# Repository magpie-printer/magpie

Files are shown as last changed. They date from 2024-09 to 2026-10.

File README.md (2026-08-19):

# Magpie

The Magpie is an open source core XY 3D printer. It's mostly printed, and can largely be built of old printers that you may have already laying around.

Design is based off of an older Rolohaun Rook design, which can be found here: https://github.com/rolohaun/Rook-180

You can put a Prusa bed on it or an Ender 3 Bed, or most other beds that can mount to a piece of 2020 extrusion.

The print area is the same as an Ender 3, and you can print a Magpie on a printer as small as a Prusa Mini.

It incorporates a P1P-style Z-axis where 3 leadscrews are driven by a single NEMA 17 stepper motor.

You can use a p1p/P1s or X1 hotend for the toolhead.

Photo of the magpie 3D printer Magpie Printer

# Magpie Mod Hub

Check out community-built upgrades on the [live Mod Hub](https://magpie-printer.github.io/magpie/) (served via GitHub Pages) or browse the static files at [`mod-hub/`](mod-hub/index.html) inside this repo. The gallery is generated directly from the `Mods/` directory, so every accepted contribution automatically shows up in the showcase.

Want to publish your own mod? Follow the short submission guide in [`Mods/README.md`](Mods/README.md); it covers the required README format and how to regenerate the hub data.

# BOM

**BOM AVAILABLE HERE**

https://docs.google.com/spreadsheets/d/1rcG37SRJA-JKYnLYInnxDPbj7JWwB8L_99AdPJc4EQ8/edit?usp=sharing

It cost me about $200 for me to build one self sourced, but your mileage may vary. I got the price down by buying dead Ender 3's on Facebook marketplace.

# Print Your own T-Shirt

The Magpie is a new project, and I can't afford to be making T-shirts and handing them out to everybody that wants them (Though I'd like to) Still, there's no reason I can't give you the files to make one for yourself! https://drive.google.com/file/d/1uzCCMDghiNLJrrfc_lJbdbuVM2ewp0ao/view?usp=sharing


# DISCORD

**JOIN US ON DISCORD**

https://discord.gg/zkxYRuTDAA

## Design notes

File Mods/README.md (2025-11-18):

# 🐦 Magpie Mods

This directory is for user-created modifications and improvements for the [Magpie CoreXY 3D Printer](https://github.com/your-username/magpie-printer-project).

We encourage the community to contribute their own designs to enhance the functionality, aesthetics, or performance of the printer.

## 💡 How to Submit a Mod

To keep this repository organized and accessible, please follow these guidelines when submitting your mod:

### 1.  **Create a New Folder**
 All files for a single mod must be contained within a new folder. Please give your folder a descriptive name (e.g., `toolhead_fan_shroud`, `led_strip_mount`, `z-chain-mount`).

### 2.  **Provide a README.md** 
Inside your mod's folder, include a `README.md` file. The Mod Hub scrapes the first heading, first paragraph, and a `Made by:` line, so format your document accordingly. At minimum include:
    * A brief description of what your mod does (first paragraph after the title becomes the card summary).
    * A list of any additional hardware required (screws, nuts, wires, etc.).
    * Simple assembly instructions.
    * Any known issues or special considerations.
	* The name of the submitting author prefixed with `Made by:` so credit appears correctly.

### 3. ** PLEASE Include `.step` Files In your submission ** 
**We require all part files to be submitted in the `.step` format. You can include other things if you want, but STEP has to be in there!**

#### **Why STEP?**

The Magpie project is built on the principle of open collaboration and easy modification. By using the `.step` format, we ensure that every user can:
  * **Freely Modify:** Edit the parts in any major CAD software (Fusion 360, SolidWorks, Onshape, FreeCAD, etc.) without losing design history or running into proprietary format issues.
  * **Learn and Improve:** Analyze the part designs to understand how they work and invent new, better parts for the printer.
  * **Maintain Compatibility:** Avoid problems with different versions of software and proprietary file formats.

 **Note:** Please do not submit `.stl`, `.3mf`, or other mesh files in lieu of a proper STEP file.
 <br>
     – These files are useful for printing but are difficult to modify and are counter to the project's goal of easy design collaboration.

-----
## ⚖️ License

All mods submitted to this folder are subject to the same license as the main Magpie printer project. By submitting a pull request, you agree to this.

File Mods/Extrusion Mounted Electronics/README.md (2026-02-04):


# Extrusion Mounted Electronics

## Summary
Mount electronics to the rear extrusion of the Magpie so you don't have to laser cut acrylic.

Made by: SpiteDriven
Links: https://github.com/owenwvaughn
Version: _No response_

## Details

You'll need: 
m3 hex nuts
m3 T-Nuts
A drill





DISCLAIMER: This mod was made using CAD assets from the following github repos and webpages:

https://github.com/Creality3DPrinting/Ender-3/tree/master   

https://github.com/bigtreetech/BIGTREETECH-SKR-mini-E3 

https://grabcad.com/library/raspberry-pi-5-2  

https://www.printables.com/model/281390-big-tree-tech-u2c-rough-cad-model/files

Download files here:
[Extrusion Mounted Electronics Mod.zip](https://github.com/user-attachments/files/25083196/Extrusion.Mounted.Electronics.Mod.zip)

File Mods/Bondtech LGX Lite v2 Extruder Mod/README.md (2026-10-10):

# Bondtech LGX v2 Extruder Mod

This mod allows you to use the Bondtech LGX v2 Extruder on the Magpie.


**DISCLOURE: This mod was made using the LGX Lite v2 model from Bondtech's site: https://www.bondtech.se/product/lgx-lite-v2-large-gears-extruder/
the thumbnail was made using lex reman's grabcad model found here:** https://grabcad.com/library/lgx-lite-1


# BOM:

**You'll need to print the Toolhead belt Connector and the x-carriage front files provided in the plated parts file.**

11  M3 nuts    
5  M3x12 bolts
 
3 MORE m3x12 bolts (If you want to use the umbilical guide) 

# Assembly

Assembly is similar to standard Magpie toolhead, but you mount two the extruder to the toolhead belt connector with two  m3x12 bolts, and then mount the toolhead connector to the x-carriage front with three m3x12 bolts. 
As is typical, you'll need to embed hex nuts wherever a hexagonal hole is in on the printed parts.
The x-carriage front also has two places to slide a hex nut into at the top. 

Made by: [https://github.com/owenwvaughn](https://github.com/owenwvaughn)

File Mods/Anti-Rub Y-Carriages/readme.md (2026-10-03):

# Anti-Rub Y-Carriage Mod

This mod serves to fix belt rubbing issues on some people's magpies. If you have that issue, this mod is for you.


**DISCLOURE: This mod will almost certainly require supports even though the vanilla versions of Magpie parts do not require supports.

# Assembly

Assembly should be no different from the regular y-carriages on a Magpie.

Made by: [https://github.com/owenwvaughn](https://github.com/owenwvaughn)

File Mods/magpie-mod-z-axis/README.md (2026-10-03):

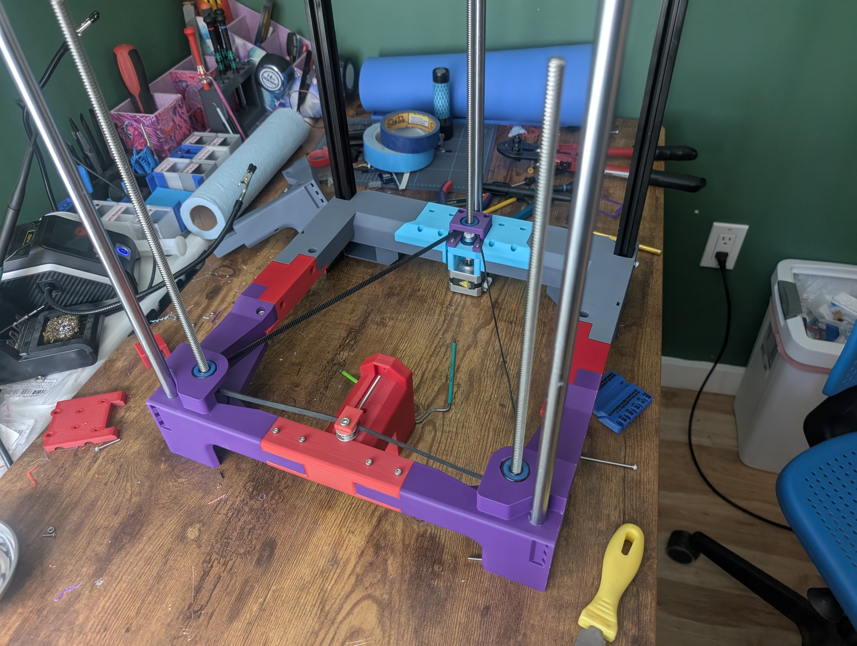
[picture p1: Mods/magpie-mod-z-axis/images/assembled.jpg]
photo of completed build, front parts shown are prototypes


# Improved Magpie Z-Axis
This mod was made to fix the issues I had with the stock z-axis design and allow for re-use of more ender 3 parts -- the z motor and lead screws. This is achieved in the front by replacing the bottom KLF-08 bearings with 2 608 bearings. This makes all three lead screws secure enough that the pulling from the belt doesn't flex the lead screws removing the need to support the front lead screws on the top frame which means the lead screws can be shorter.
 
In the rear, a spacer and two additional 608 bearings are added: The spacer allows enough space to add a coupler to attach the lead screw to the motor shaft and the bearings -- like in the front -- secure the lead screws to not flex from the belt tension. 

Because the belt path does not change, there is a small loss of ~5-8mm of z travel. This could be fixed by lowering the belt path however, that would require changes to the tensioner parts as well. I wanted to keep this mod as minimal as possible to reduce needed reprinting so I chose to keep the same belt path. Lowering the belt path may also impact clearance on the back for larger pulleys.

## BOM
### Hardware
| Name | Qty | Note |
|:---:|:---:|:---:|
| 608 bearing | 6 | fushi brand recommended |
| M3x45mm bolts | 4 | for motor mount |
| 5x8mm coupler | 1 | reused from ender 3 |
| motor | 1 | reused from ender 3 |
### Printed Parts 
| Name | Qty |
|:---:|:---:|
|  zcorner_R  | 1 |
|  zcorner_L  | 1 |
| motor_spacer_25mm | 1 |
| Z-axis_mod-Coupling_box | 1 |
| spacer_bottom | 2 |
| spacer_top | 2 |

## Assembly
Place the parts on the leadscrew in this order:
1. 608 bearing
2. top_spacer with the larger chamfer side toward the bearing (up)
3. pulley in upright position
4. bottom spacer with the larger chamfer side toward the bearing (down)
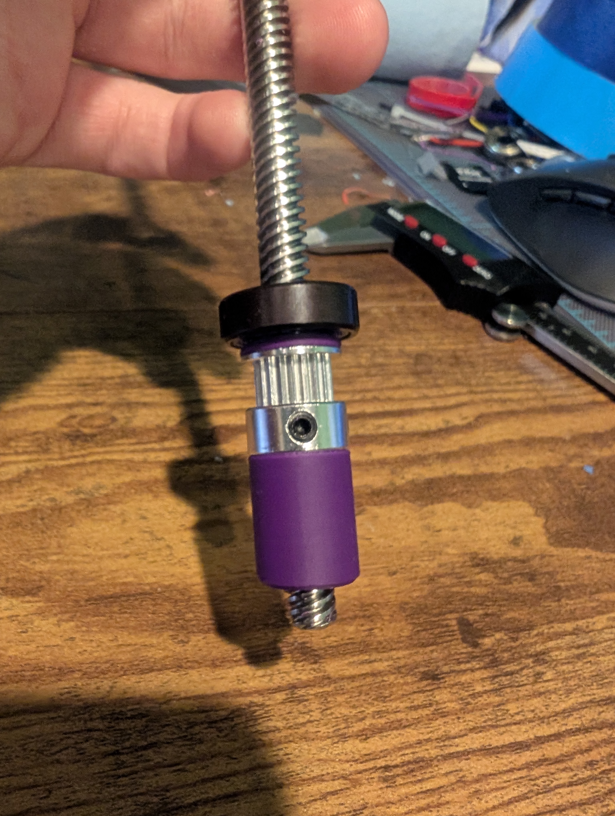
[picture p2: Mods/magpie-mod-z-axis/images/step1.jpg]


place the bottom bearing on the lead screw and align the stack so the lead screw is slightly proud of the bottom bearing when fully seated


remove the bottom bearing from the stack and insert it into the zcorner part


place the stack on the zcorner part and make sure the belt is around the stack


push the top bearing into place on the zcorner part


move the belt onto the pulley and tighten the set-screws


unfortunately i didn't take photos of the rear assembly so this will be primarily text:

1. place the coupler on the motor shaft
2. place the spacer on the motor
3. place the motor and spacer under the motor mount
4. insert the lead screw into the motor coupler and tighten the coupler to both the lead screw and motor shaft
5. optionally use M3x40mm screws to attach the motor through the spacer to make the next step easier
6. press a 608 bearing into the motor mount while keeping the motor and spacer against the bottom of the mount
	- if the 608 bearing sticks out more than 1-3mm, remove it and continue to the next step
	- if the bearing sticks out less than 1-3mm, loosen the coupler and move onto the next step
	- if you did step 5, remove those screws before the next step
7. remove the lead screw from the motor coupler
8. place the coupling box on the motor mount and screw the motor in using the M3x45mm bolts
9. press a 608 bearing into the coupling box
10. place the pulley on the belt and push it into the position in the image
11. insert the lead screw through the top bearing, pulley and bottom bearing (if there is one) into the coupler
12. push the coupler onto the lead screw until it either is fully seated or has a 1mm gap between the coupler and bottom bearing then tighten the coupler
13. align the pulley to the belt path and/or front pulleys then tighten the set-screws
14. Congratulations, you have finished assembling this mod!
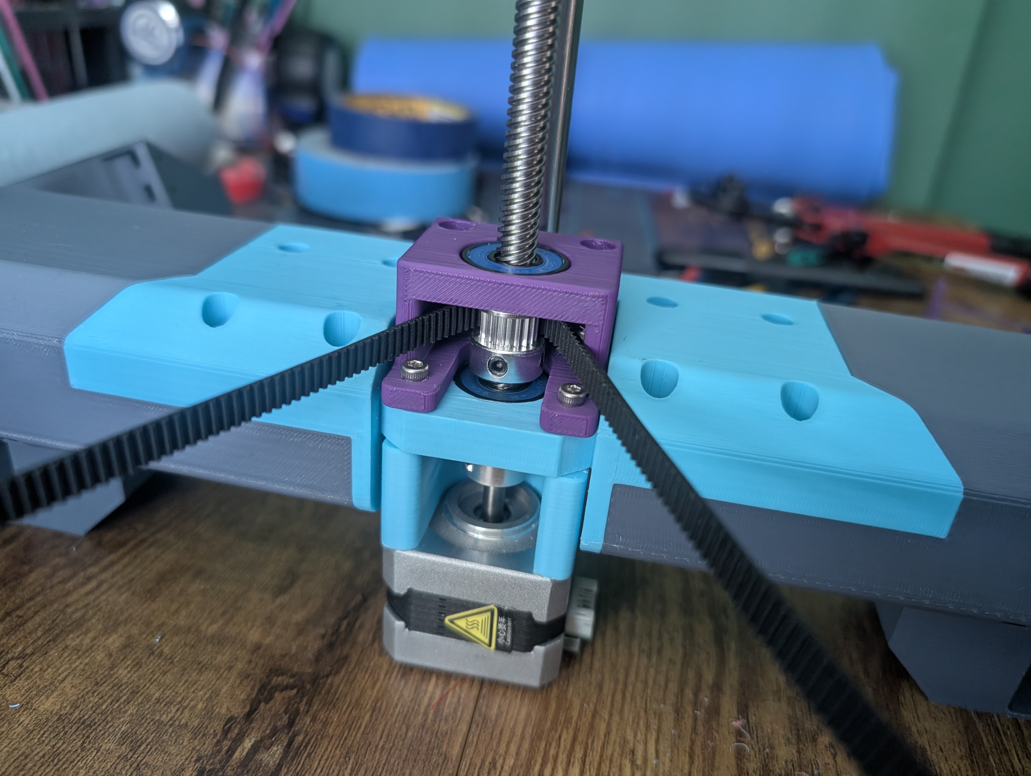
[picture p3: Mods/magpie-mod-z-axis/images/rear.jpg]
rear assembled


## Atrribution
The part `Z-axis_mod-Coupling_box` was taken from rowokii's z axis mod found [here](https://github.com/magpie-printer/magpie/blob/main/Mods/Z-Axis%20Lead%20Screw%20Mod/Z-axis_mod-Coupling_box.step) and modified to take non-countersunk bolts and be shorter to fit the needs of this mod.

# Credit
Made by: piegolf

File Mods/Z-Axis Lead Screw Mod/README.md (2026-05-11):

# Z Axis - Lead Screw Mod

Magpie BOM calls for NEMA 17 stepper motor with a 400mm lead screw integrated into it. 

This mod allows you to use a standard NEMA 17 stepper motor with a separate lead screw.  Since most couplers do not handle lateral force well, this mod supports the lead screw with two 608 bearing and the stepper motor drives the lead screw with a loop belt.  

z-axis_mod_top 

This design was "optimized" to use parts I had in hand.

# BOM:

You need to 3d print the three step files.  They do not need supports if oriented as shown. 
Printed Parts

 I used typical "Voron" print settings of .2mm layer height, .4mm line width, 4 walls, 5 top/bottom shell with 40% cubic infill .

You also need the below hardware: 

| #  | Item |  Description | 
| :---:  | :--- | :---|
| 4 | FHM3x30 | M3 flat head screw - 30mm long |
| 4 | M3x16 | M3 button head or socket head screw - 16mm long |
| 4 | M3 nuts | M3 nuts |
| 4 | M3 washer | M3 washer
| 2 | 608 Bearing | 608 Skate Bearing |
| 1 | GT2 20T 8mm | 20T GT2 Pulley with 8mm bore, 6mm width (You need 1 more than called by Magpie BOM) |
| 1 | GT2 20T 5mm | 20T GT2 Pulley with 5mm bore to be used with NEMA 17 stepper motor, 6mm width |
| 1 | GT2 - 160mm belt | GT2 loop belt 160mm long, 6mm wide |
| 1 | NEMA 17  | NEMA 17 Stepper motor for your Z axis | 
| 1 | 8mm Lead Screw | 8mm Lead Screw (1/3 lead screw from the BOM) |
| | | |

<br>
<br>

# Assembly

Press the 608 bearing in to the round hole in the "Rear_Bottom_Back.step" where the round part of the NEMA17 motor would normally press into.  Motor_mount is placed below and Coupling box is place above, trapping the 608 bearing.  Screw the parts together using FHM3x30 screw and m3 nuts.

Rear_Bottom_Back_assembly 

Lead screw, the spacer block, GT2-20T-8mm and another 608 bearing is assembled as shown.  You need to have the 1M belt in the stack as well.  Do not tighten the grub screw on the GT-20T-8mm yet.

top_assembly

The NEMA 17 stepper motor is held in place with four M3x16 screws with washers.  GT2-20T-8mm pully is locked into place at the end of the lead screw.  Loop the GT2-160mm belt onto the GT2-20T-8mm and GT2-20T-5mm and press the GT2-20T-5mm onto the shaft of the NEMA 17 Stepper.  Tension and lock the motor in place and tighten all grub screws, including the one in the coupling box.

bottom_assembly

There is nothing holding down the 608 bearing at the top of the coupling box except fit friction and from the 1M belt loop tension, but after few hundred hours of print, I don't find this to be a problem.

Made by: https://github.com/rowokii

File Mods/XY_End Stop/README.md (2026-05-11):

# X/Y Endstop Switches

Default for Magpie is to use sensorless homing.  Since my controller board had the older step drivers that does not support sensorless homing, I added limit switches for X/Y endstops.  Any micro switches that has mounting holes 6.5mm apart should work fine.
M2 bolts are used to directly thread into the plastic to mount the switches

The current x-carriage_rear has mounting holes for X-end stop.    Xy_endstop_bumper is used to add a bumper to the Y-carriage_right so the limit switches activates without crashing the X or Y carriage. 

X_limit_switch_bumper

Back_rod_holder was slightly modified to have mounting holes for the Y end stop switch.

Y_limit_switch_bumper

Made by: https://github.com/rowokii

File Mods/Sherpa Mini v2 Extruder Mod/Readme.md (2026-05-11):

# Magpie Toolhead – Sherpa Mini V2 Compatible Mod 



## Overview

Lets you use a sherpa mini v2 with your Magpie

1. **Modified toolhead midbody** with mounting holes for the Sherpa Mini V2  
2. **Modified belt connector piece** with one side extended

Assemble this toolhead as you normally would, but **use a Sherpa Mini extruder** instead of the stock extruder.  
You will still need the **standard rear body** and **front cover** from the main Magpie’s plated parts folder.

---

## Required Hardware

To mount the Sherpa Mini V2 extruder to this toolhead revision, you will need:

- **1× Sherpa Mini V2**
- **2× M3 hex nuts**
- **2× M3×20 bolts**

---

## Printing Notes

The plated parts STL can be dropped into any slicer and is already oriented correctly.

**No supports are required.**

---

## Credits

Made by **SpiteDriven**  
<https://github.com/owenwvaughn>

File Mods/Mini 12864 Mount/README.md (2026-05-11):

# Mini 12864 Mounting bracket

A simple mounting bracket for mounting a [MINI 12864 LCD Display Housing for 2020 V-slot](https://www.printables.com/model/56150-mini-12864-lcd-display-housing-for-2020-v-slot) to the Magpie bottom front connector block.  M3x35 bolts are replaced with longer (M3x40 or 45) to bolt the bracket as shown.

My Mini 12864 reset button was too long to fit into the case, so I simply drilled out a hole in the case to fit.

Mini 12864 on Magpie

Bracket

Made by: https://github.com/rowokii

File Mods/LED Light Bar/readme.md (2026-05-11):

# LED Light Bar, light bar brackets and USB Camera bracket

I mostly use my printers remotely.  Having extra lights so I can see the printer with my web cam is nice. 

The light bars are attached using brackets to extra mounting holes.  It may interfere if you want to have a top hat/ side panels. Straight bracket is used in the front and two different size back brackets for the left and right rear.  

The camera bracket is a simple L bracket I used to velcro tie monitor mounting usb web camera.

LED BAR

Made by: https://github.com/rowokii

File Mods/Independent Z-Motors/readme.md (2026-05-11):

thumbnail

# Independent Z-Motor Mod

This mod allows users to use independent Nema 17 stepper motors to control Z-movement, and therefore allows for Z-tilt like a Voron Trident.

## DO NOT USE LINEAR BEARINGS FOR THE Z-AXIS RODS AS THEY WILL CAUSE BINDING, BUT YOU STILL NEED THE RODS THEMSELVES FOR STRUCTURE.
IN FACT DON'T EVEN USE THE BEARING CLAMPS

# Bill of Materials:

Non-printed parts:
 - Z motors w/ 400mm integrated leadscrews **x3**
 (that's the 1 the vanilla uses + the 2 this mod uses for a total of 3)
 - M3x14 Socket Cap Screw ***x8***
 - Laser cut acrylic bottom panel (independent motor version) ***x1***

Printed parts:

 - Right Z motor mount

 - Left Z motor mount

 *Print with 4 walls, 5 on top, 5 on bottom, 40% infill in a pattern of your choosing out of ABS or PETG

## Assembly

The **Right Z motor mount** and **Left Z Motor mount** replace the normal front bottom corners of the Magpie, and attach to the frame in exactly the same way as the parts that they replace. The only thing extra you'll need to do is to mount the Z motors to them using the 4 mounting holes each of the parts has. The motors are mounted with M3x14 Socket Cap Screws. 
Assembly Diagram
The final thing to note is that since you're no longer using a belt for the Z axis, you can feel free to completely omit the printing, assembly, and/or requisition of the following parts:

 - Tensioner Extension
 - Tensioner Idler holder
 - Thumb Tensioner
 - 1M GT2 closed loop belt

## Pictures
real photograph of part
bottom_side_pic
## Credits

Made by **SpiteDriven**  
<https://github.com/owenwvaughn>

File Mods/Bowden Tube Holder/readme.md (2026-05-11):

# Clip On Reverse Bowden Tube Holder

This mod lets you clip one end of your bowden tube to the sides of the Magpie top frame. 
Designed to friction fit with a standard PTFE tube. Useful for open frame Magpie printers. 


## Credits
Made by **flymolo92**  
<https://github.com/flymolo92>

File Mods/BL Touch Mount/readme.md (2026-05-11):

# BL Touch Mount

Simple mount bracket to attach BL Touch to the back of the Magpie's Tool head.

BL Touch Mount

The x_carriage_rear has two M3 threaded insert attachment points.  The mount is attached to the x carriage with two M3 screws and has room for slight adjustment up or down.   

BL Touch is attached to the mounting bracket with two M3 screws directly into the printed part.

I printed the mount oriented as shown, with support.  

BL Touch Mount orientation

BL Touch has the following XY offset for my build.

x_offset: 0<br>
y_offset: 35

Made by: https://github.com/rowokii

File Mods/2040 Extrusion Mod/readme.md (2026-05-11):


# 2040 Extrusion Mod

This mod replaces the 400mm 2020 extrusion on the rear of the Magpie with 400mm 2040 extrusion. 
Why? because it makes it easier for people to convert Ender 3's into Magpies, and that's always a good thing. 

This mod will pair nicely with the following mods if you're coming from an Ender 3: 

 - [X/Y Endstop
   Switches](https://github.com/magpie-printer/magpie/blob/main/Mods/XY_End%20Stop/README.md)
 - [Z Axis - Lead Screw
   Mod](https://github.com/magpie-printer/magpie/blob/main/Mods/Z-Axis%20Lead%20Screw%20Mod/README.md)

# Bill of Materials:

Just use 400mm long 2040 extrusion and the printed parts here instead of  400mm long 2020 extrusion and the regular Magpie parts. 
parts should be printed with the following settings:

 *Print with 4 walls, 5 on top, 5 on bottom, 40% infill in a pattern of your choosing out of ABS or PETG

## Pictures


## Credits

Made by **SpiteDriven**  
<https://github.com/owenwvaughn>

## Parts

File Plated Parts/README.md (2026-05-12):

# Plated Parts

STL files for all printed parts of the Magpie printer.

## Print Settings

Use the VORON STANDARD profile for all parts:

- Layer height: 0.2mm
- Extrusion width: 0.4mm (forced)
- Infill: 40%
- Infill type: Grid, gyroid, honeycomb, triangle, or cubic
- Wall count: 4
- Solid top/bottom layers: 5
- Supports: NONE

These settings are specified in the build guide.

## Materials

Acceptable: ASA, ABS, PETG, PCTG, PLA

Don't enclose a PLA printer. If you want an enclosed build, use ABS, PETG, or ASA instead.

## Print Order

Print in this order:

### 1. Frame

`top_frame_corner_pieces.stl`  
`top_frame_connecting_pieces.stl`  
`Bottom_frame_corner_pieces.stl`  
`Bottom_frame_connecting_pieces.stl`

The frame parts are printed first. They form the main skeleton of the printer and take the longest to print.

### 2. Motion System

`X&Y_Motion_Parts.stl`  
`z_axis_parts.stl`

Print after the frame is done. The motion parts need to be accurate, so make sure there are no layer shifts.

### 3. Toolhead

Choose one based on your extruder:

`Toolhead/toolhead_pieces_Sherpa_mini.stl` — For Sherpa Mini v2  
`Toolhead/toolhead_pieces_Orbiter2.stl` — For Orbiter 2  

You can also use P1P or X1 hotends with the right adapter.

### 4. Enclosure (Optional)

`Enclosure/enclosure_lid_parts.stl`  
`Enclosure/Door_parts.stl`

Optional. The enclosure improves thermal control and reduces noise, but the printer works without it.

### 5. Precision Shim

`Printable Precision Shim/`

Print these only if you need them for bed leveling during final assembly.

## Timing

Total print time is 200-350 hours depending on whether you print the enclosure. This assumes continuous printing. If you have multiple printers, you can speed this up by printing parts in parallel.

## References

- Assembly instructions: `../Build Guide/build_guide.pdf`
- CAD source files: `../cad/` (FreeCAD format, can be edited and re-exported)
- BOM (hardware, electronics, fasteners): https://docs.google.com/spreadsheets/d/1rcG37SRJA-JKYnLYInnxDPbj7JWwB8L_99AdPJc4EQ8/edit?usp=sharing
- Questions? Ask in the [Discord](https://discord.gg/zkxYRuTDAA)

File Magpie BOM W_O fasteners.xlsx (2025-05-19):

Component Name | Quantity
F695 Bearing | 16
M5-Washer (printing washers works, don't tell anybody it's a secret) | 14
GT2 20T Pulley 6mm | 2
GT2 20T Pulley 8mm | 3
320mm long Linear Rod, 8mm Diameter | 4
400mm long Linear Rod, 12 mm in diameter | 3
400mm long Aluminum Extrusion (20mm x 20mm | 2
400mm long 8mm diameter leadscrew | 2 (3 if you're not using the z motor with a leadscrew coming out of it)
Nema 17 with 400mm long Leadscrew coming out of it. | 1
KLF08 Bearings | 2
GT2 Toothless bearing with a 5mm inner bore (or just use2 more F695 Bearings | 1
300mm Long 2020 Extrusion | 1
280mm Long 2020 Extrusion | 1
Square Corner Brackets | 6
8mm POM Nut | 3
Ender 3 Bed | 1
Ender 3 bed mount | 1
LM12UU Linear Bearing | 3
Nema 17 Motor | 2
Ender Power supply, or other power supply | 1
Laser cut acrylic bottom panel | 1
Orbiter 2 Extruder | 1
Bambu lab hotend or third party equivelant | 1
Super Pinda Z-probe or equivelant | 1
LM8UU | 6
4010 Blower Fan | 2
3010 Fan | 1

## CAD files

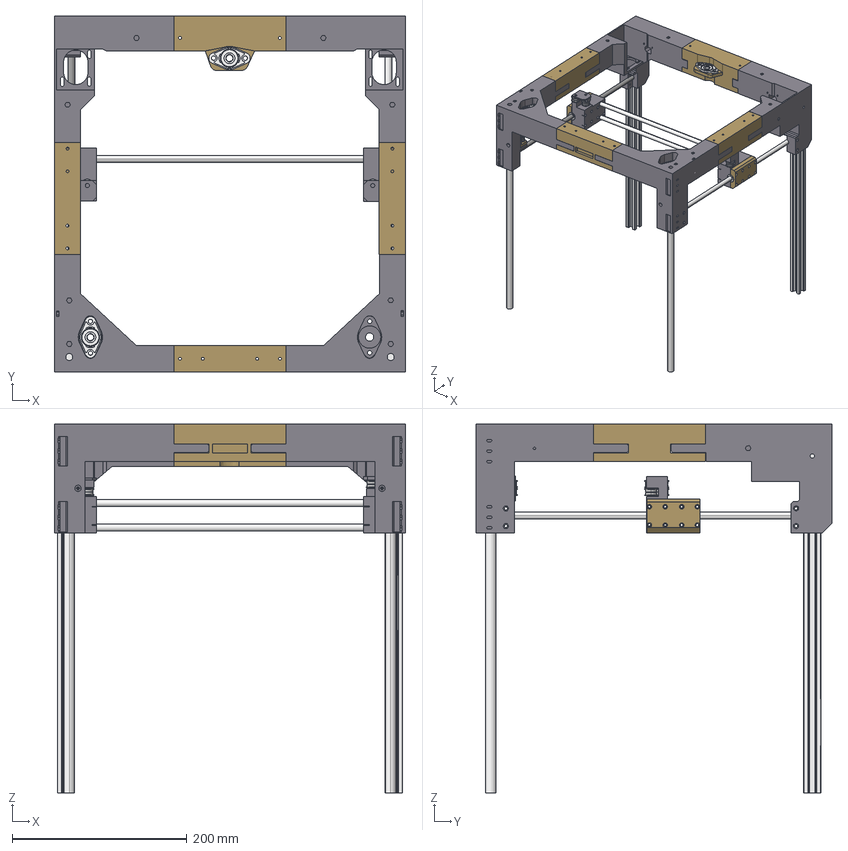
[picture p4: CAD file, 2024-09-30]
cad/assembly.FCStd
402.3 x 407.6 x 422.9 mm
TOP_Right_Rear_Frame
Rear_upper_central_brace
frame_top_extender
TOP_Left_Rear_Frame
frame_top_extender2
8mm Linear Rod 350mm
8mm Linear Rod 360mm001
8mm Linear Rod 360mm
Top_left_front_frame1_001
Top_magnet_extender1_001
TOP_Right_Front_Frame_001
8mm Linear Rod 350mm001
Left_Idler_Cartridge1_001
Right_Idler_Cartridge1_001
M5 precision shim
F695 Bearing001
M5 precision shim001
F695 Bearing002
F695 Bearing003
M5 precision shim002
F695 Bearing
M5 precision shim003
F695 Bearing005
M5 precision shim004
F695 Bearing006
F695 Bearing007
M5 precision shim005
F695 Bearing004
BEARING B002
BASE002
BEARING A002
BEARING C002
Y_carriage_left_001
LM8UU_
LM8UU_2
LM8UU_003
LM8UU_004
Y_clamp_001
Y_clamp_002
Y_carriage_right_001
F695 Bearing008
F695 Bearing009
M5 precision shim006
M5 precision shim007
F695 Bearing010
F695 Bearing011
M5 precision shim008
M5 precision shim009
F695 Bearing012
F695 Bearing013
M5 precision shim010
M5 precision shim011
F695 Bearing014
F695 Bearing015
M5 precision shim012
M5 precision shim013
vslot-extrusion-20mmx20mmx400
vslot-extrusion-20mmx20mmx400_
BEARING B003
BASE003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

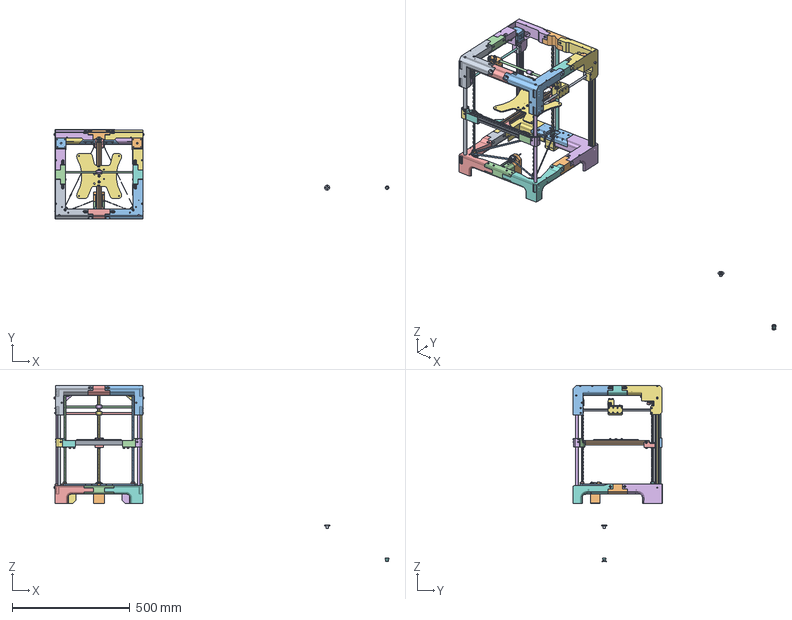
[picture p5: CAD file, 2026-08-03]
Build Guide (work in progress)/FreeCAD Build_guide_Staging_file/build_guide_WIP.FCStd
1424.2 x 380.6 x 749.1 mm
M5-Nut1639
M5-Nut1640
M5-Nut1641
M5-Nut1642
M5-Nut1643
M5-Nut1644
M5-Nut1645
M5-Nut1646
Bottom_frame_side_connector
Bottom_frame_side_connector_02
Rear_bottom_back_frame
Front_frame_tensioner
bottom_front_left_frame
Rear_Right_Bottom_frame
Rear_left_Bottom_frame
bottom_front_Right_frame
idler_holder_001
Tensioner_extension
M3-Nut4599
M3-Nut4600
M3-Nut4601
M3-Nut4602
M3-Nut4603
M3-Nut4604
M3-Nut4605
M3x20-Screw115
M3x20-Screw116
M3x35-Screw051
M3x35-Screw052
M3x35-Screw053
M3x35-Screw054
M5x25-Screw1844
M5x25-Screw1845
M5x25-Screw1846
M5x25-Screw1847
M5x25-Screw2038
M5x25-Screw2039
M5x25-Screw2040
M5x25-Screw2041
M3-Nut4975
M3-Nut4976
M3-Nut4977
M3-Nut4978
M3-Nut4979
M3-Nut4980
M3-Nut4981
M3-Nut4982
M3x25-Screw237
M3x25-Screw238
M3x25-Screw239
M3x25-Screw240
M3x25-Screw241
M3x25-Screw242
M3x25-Screw243
M3x25-Screw244
GT2 20T Pulley 8mm v2_004
8mm Pom Nut 001
M5-Nut1772
M5-Nut1773
M5-Nut1774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

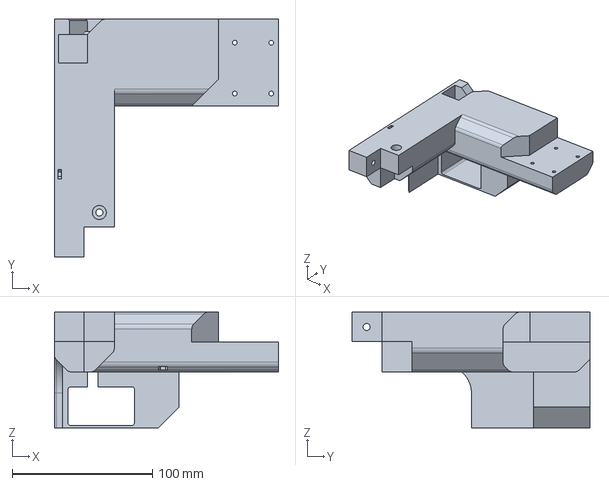
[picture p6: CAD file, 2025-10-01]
cad/A2Plus References/Rear_left_bottom_frame.FCStd
160.0 x 169.7 x 82.7 mm

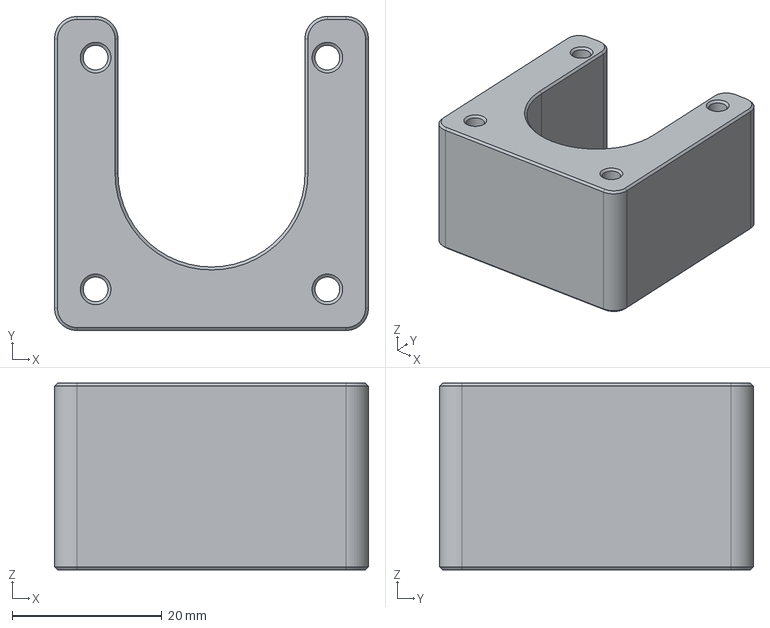
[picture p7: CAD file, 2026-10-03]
Mods/magpie-mod-z-axis/CAD/motor_spacer_25mm.step
42.0 x 42.0 x 25.0 mm

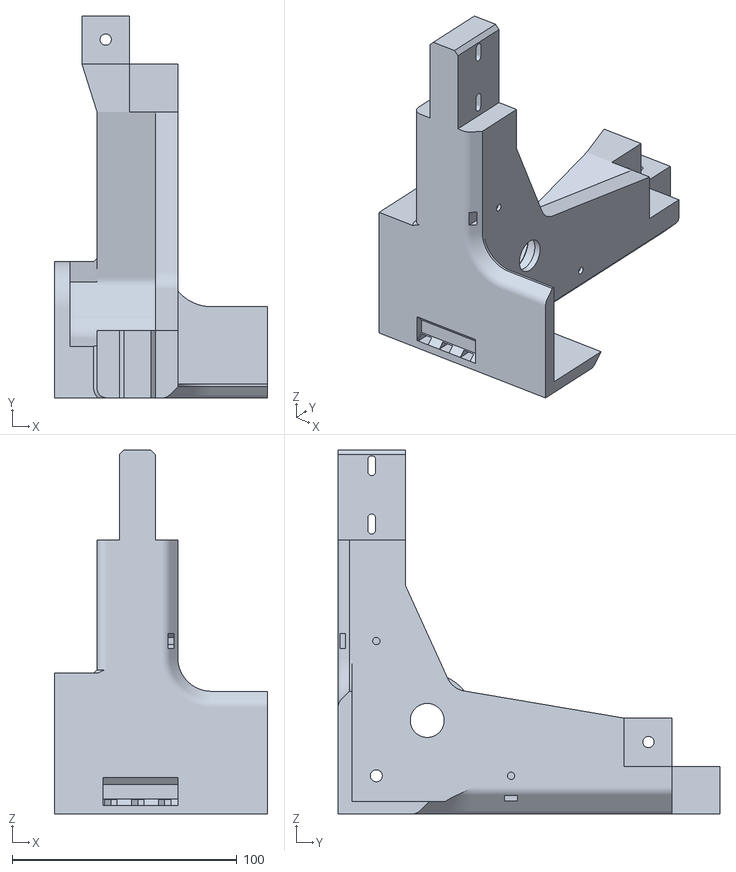
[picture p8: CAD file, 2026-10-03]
Mods/magpie-mod-z-axis/STL/zcorner_L.stl
95.0 x 170.0 x 162.1

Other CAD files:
Mods/Independent Z-Motors/CAD Assemblies/Assembly.step
cad/Magpie_revision_1/Magpie_Rev_1.step
Mods/2040 Bed Connector/beefy_rear_coupler.step
Mods/2040 Extrusion Mod/CAD/2040_Extrusion_Mod.step
Mods/2040 Extrusion Mod/STL/Rear_bottom_Left.step
Mods/Anti-Rub Y-Carriages/anti_rub.step
Mods/Attachable Spool Holder/spool_holder-Spool_holder.step
Mods/BL Touch Mount/BLTouch_Mount.step
Mods/Bondtech LGX Lite v2 Extruder Mod/LGXlite umbilical guide.step
Mods/Bowden Tube Holder/Reverse_bowden_holder.step
Mods/Extrusion Mounted Electronics/BTT e3 SKR mini_mount.step
Mods/Independent Z-Motors/Right Z Motor Mount.step
Mods/LED Light Bar/Cam_Mount.step
Mods/2040 Bed Connector/2040_bed_connector_rear_001.step
Mods/2040 Extrusion Mod/CAD/2040_Extrusion_Mod.FCStd
Mods/2040 Extrusion Mod/STL/Rear_bottom_Right.step
Mods/2040 Extrusion Mod/STL/Rear_top_Left.step
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

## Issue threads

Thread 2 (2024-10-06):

`Z Stepper Motor` intersects `Leadscrew_mount_back_001`

lucian151, 2024-10-06:
This collision between the Leadscrew_mount_back_001 and motor needs to be addressed:
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

owenwvaughn, 2024-10-07:
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

Closed 2024-10-07.

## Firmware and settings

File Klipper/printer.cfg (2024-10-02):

[include mainsail.cfg]
[include pinout_aliases.cfg]
[include mks_mini_12864_v3.cfg]
[exclude_object]
#[include adxl.cfg]

[printer]
kinematics: corexy
max_velocity: 600
max_accel: 7500 # change this to 7500 after commissioning
max_z_velocity: 3   # may be able to increase to 15 after comissioning.
max_z_accel: 50
square_corner_velocity: 5 # start at 8, but then increase once you're sure assembly is sound

[mcu] 
serial: /dev/serial/by-id/usb-Klipper_stm32f407xx_350050001251323439393937-if00


[gcode_macro CALIBRATE_BED_LEVEL]
gcode:
  G28
   BED_MESH_CALIBRATE

[gcode_macro PRINT_START]
#   Use PRINT_START for the slicer starting script - PLEASE CUSTOMISE THE SCRIPT
gcode:       
    CALIBRATE_BED_LEVEL

## Wipe Macro####


# Stepper Configs
[stepper_x]
# connected to X Stepper
step_pin: PC14
dir_pin: !PC13
enable_pin: !PC15
rotation_distance: 40
full_steps_per_rotation: 200
microsteps: 32
endstop_pin: tmc2209_stepper_x:virtual_endstop 
position_endstop: 243
position_min: 0
position_max: 260
homing_speed: 100
homing_retract_dist: 0

[tmc2209 stepper_x]
# connected to X Stepper
uart_pin: PE6
run_current: 0.9 #was .9
sense_resistor: 0.110
#stealthchop_threshold: 999999
interpolate: False #was false
diag_pin: PA14
driver_SGTHRS: 170

[stepper_y]
# connected to Y Stepper
step_pin: PE5
dir_pin: PE4
enable_pin: !PC15
rotation_distance: 40
full_steps_per_rotation: 200
microsteps: 32
endstop_pin: tmc2209_stepper_y:virtual_endstop
position_endstop: 230
position_max: 230
homing_speed: 100
homing_retract_dist: 0

[tmc2209 stepper_y]
# connected to Y Stepper
uart_pin: PE3
run_current: 0.9 #was .9
sense_resistor: 0.110
#stealthchop_threshold: 999999
interpolate: False #was false
diag_pin: PA15 
driver_SGTHRS: 170

[stepper_z]
step_pin: PE1
dir_pin: PE0
enable_pin: !PE2
rotation_distance: 2
full_steps_per_rotation: 200
microsteps: 32
endstop_pin: probe:z_virtual_endstop
position_min: -10
position_max: 150
homing_speed: 100
homing_retract_dist: 10


[tmc2209 stepper_z]
# connected to Z Stepper
uart_pin: PB7
run_current: 0.9
sense_resistor: 0.110
#stealthchop_threshold: 999999
interpolate: False #was false
diag_pin: PB13



# Extruder0
[extruder]
# connected to E4 Stepper
step_pin: PD13
dir_pin: !PD12
enable_pin: !PB6
rotation_distance: 4.4637
microsteps: 16
full_steps_per_rotation: 200
nozzle_diameter: 0.400
pressure_advance: 0.03
pressure_advance_smooth_time: 0.040
filament_diameter: 1.750	

# connected to TH0
sensor_type: ATC Semitec 104GT-2
sensor_pin: PC1

min_extrude_temp: 0
min_temp: -200
max_temp: 999
# connected to HE0
heater_pin: PB1
max_power: 1.0
max_extrude_only_distance: 1400.0
max_extrude_only_velocity: 120.0
max_extrude_only_accel: 1500.0
max_extrude_cross_section: 20000.0

[tmc2209 extruder]
# connected to E4 Stepper
uart_pin: PD11
run_current: 0.4
sense_resistor: 0.110
#stealthchop_threshold: 0
interpolate: False


# connected to Heater0
# Fans  
# Hotend Cooling Fan
[heater_fan my_nozzle_fan]
# connected to Fan0 - 24v Fan
pin: PA2
max_power: 1.0
#kick_start_time: 0.5
heater: extruder
heater_temp: 50.0
 
# print cooling fan
[fan]
# connected to Fan1 - 12v Fan
pin: PA0
max_power: 1.0
kick_start_time: 0.500



[heater_bed]
heater_pin: PB10
sensor_type: Generic 3950
sensor_pin: PC0
max_power: 1.0
min_temp: 0
max_temp: 120

[input_shaper]
shaper_freq_x: 0
shaper_freq_y: 0
shaper_type: mzv

[probe]
#Z_offset: 0.0
pin: PA8


[bed_mesh]
speed: 60
horizontal_move_z: 5

mesh_min: 20, 35
mesh_max: 200, 220
probe_count: 4, 4

[safe_z_home]
home_xy_position: 115, 115 # Change coordinates to the center of your print bed
speed: 50
z_hop: 0                 # Move up 10mm
z_hop_speed: 5


#Gcode G2/G3 Arc Support
[gcode_arcs]
resolution: 0.1

# Motor and Heater Idle Timeout
[idle_timeout]
timeout: 6000

[respond]

#*# <---------------------- SAVE_CONFIG ---------------------->
#*# DO NOT EDIT THIS BLOCK OR BELOW. The contents are auto-generated.
#*#
#*# [extruder]
#*# control = pid
#*# pid_kp = 43.538
#*# pid_ki = 16.125
#*# pid_kd = 29.388
#*#
#*# [bed_mesh default]
#*# version = 1
#*# points =
#*# 	0.301250, 0.803750, 0.634062, 0.632500
#*# 	-0.014375, 0.453125, 0.445625, 0.445000
#*# 	-0.520938, 0.086250, 0.057187, 0.155937
#*# 	-1.665938, -0.863125, -0.592500, -0.581250
#*# x_count = 4
#*# y_count = 4
#*# mesh_x_pps = 2
#*# mesh_y_pps = 2
#*# algo = lagrange
#*# tension = 0.2
#*# min_x = 20.0
#*# max_x = 200.0
#*# min_y = 35.0
#*# max_y = 219.98
#*#
#*# [heater_bed]
#*# control = pid
#*# pid_kp = 70.188
#*# pid_ki = 1.248
#*# pid_kd = 987.021
#*#
#*# [probe]
#*# z_offset = 0.885

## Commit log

2024-09-28 Adds initial CAD to and render to repo
    [magpie.step]
2024-09-30 Added parts of the printer in the freecad format.
    More of these parts will be added this week. I just want to make new parts available as soon as they can be.
    [Bottom_front_right_frame.FCStd, Left_Idler_Cartridge.FCStd, Left_Idler_Cartridge.step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]
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2024-10-02 Changed Idler Cartridges out of anger.
    Changed the dimensions of the captive nut pocket in the idler cartridges. They were a legacy dimension from the days this was a Rook Mod. 0.7mm is not enough plastic for the kind of tension you would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
    💢💢💢💢💢
    [Left_Idler_Cartridge.FCStd, Right_Idler_Cartridge.FCStd]
2024-10-02 Finished adding the Z-axis to the Freecad File.
    [Bottom_front_right_frame.FCStd, Leadscrew_mount_back.FCStd, Left_Idler_Cartridge.FCStd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]
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2024-10-07 Housekeeping of FCbak and collision fixes
    [Leadscrew_mount_back.FCStd, bed_knob.FCStd]
2024-10-08 Fixed Top connectors to have a through hole
    [frame_top_extender.FCStd]
2024-10-11 Cleaned up the STEP File, and made an F3D version
    Made an F3D version just so people wouldn't have to sit and wait for the file to open in Fusion 360
    [magpie.step]
2024-10-12 Adjusted dimensions of Freecad Assembly
    Changed the dimensions of the holes for slide in nuts in the frame.
    [Bottom_front_right_frame.FCStd, Leadscrew_mount_back.FCStd, Rear_right_bottom_frame.FCStd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]
2024-11-20 Update Y_carriage_left.FCStd
    Adjusted tolerances on y_carriage_left
    [Y_carriage_left.FCStd]
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2024-11-24 Adjusted y clamp, and cleaned up left y axis carriage
    [Y_carriage_left.FCStd, Y_clamp.FCStd]
2024-11-25 Same changes as before
    Same as previous change. It just didn't take. Ooops.
    [Y_carriage_right.FCStd, Y_clamp.FCStd]
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2025-04-10 Create Magpie_Rev_1.FCStd
    Adding work-in-progress file for revision 1 of the Magpie, which will include screws and other vitamins.
    [Magpie_Rev_1.FCStd]
2025-04-10 Update Magpie_Rev_1.FCStd
    Adding more nuts and bolts and components to the CAD File.
    [Magpie_Rev_1.FCStd]
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2025-05-05 Re-organized folders
    Made sure new version was clear and available. Exported generic step file that includes the nuts and bolts.
    [Bed_mount_center.FCStd, Bottom_frame_connector.FCStd, Bottom_front_right_frame.FCStd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]
2025-05-19 Added BOM without fasteners
    I felt so bad after talking to everybody today and saying "I don't have a BOM, but I'll have one soon."
    I don't want to wait to get you the most up to date info on the printer. So, here's everything but the screws and nuts. I'll add those eventually too, but for now this is the non-printable components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
    Thanks to everybody who showed up today at RMRFF!
    [Magpie BOM W_O fasteners.xlsx]
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2025-05-20 Made hotend more compatible with 3rd party bambu hotends
    [Magpie_Rev_1.step]
2025-05-22 Changed Toolhead Geometry
    Added a filet to the rear part of the mid-body of the toolhead so that it was easier to print without curling off of the build sheet. Then altered the rearbody of the toolhead to hide that filet
    [Magpie_Rev_1.step, Toolhead_Ears.step, Toolhead_door.step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]
2025-05-31 Updated fasteners
    M5x8-Screw032, 033, 034 and 035 were too short. Made them 25mm long.
    Also changed the T-slot nuts to be hammer T nuts.
    Friends don't let friends not know about hammer T-nuts.
    [Magpie_Rev_1.step]
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2025-08-21 Added mount for u2c board if you're using u2c board.
    [u2c_mount.step]
2025-08-21 Update u2c_mount.step
    Made the standoffs thicker to prevent snapping.
    [u2c_mount.step]
2025-09-09 Changed toolhead Z probe clearance
    changed how far down the Z probe can be screwed in to accommodate things like revo hotends or other non-standard length p1p hotends.
    [Z_probe_lowerable.FCStd]
2025-09-30 Began making basic a2p refs. Added them to parts list. It isn't everything.
    [Bottom_frame_side_connector.step, Bottom_front_connector.step, Bottom_front_left.step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]
2025-10-01 Changed a2plus references to fcstd instead of step
    [Bottom_frame_side_connector.FCStd, Bottom_frame_side_connector.step, Bottom_front_connector.step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]
2025-10-12 Added Z-Axis Lead Screw Mod
    Lead Screw Mod files and README added
    [Z-axis_mod-Coupling_box.step, Z-axis_mod-Motor_Mount.step, Z-axis_mod-Spacer.step]
2025-10-12 Updated Toolhead support for endstop mod by rowokii
    Updated the X_carriage_rear to accept the endstop mod from rowokii
    This doesn't change anything for users who aren't using mechanical endstops, but makes it easier for people who do want to use mechanical switches to simply put them on.
    Also did minor housekeeping for the assembly. It's still a mess, but it's a little bit better now.
    [Magpie_Rev_1.step]
2025-10-12 Added XY Limit switch and Mini 12864 display bracket to the MOD directory
    Additional mods added
    [Back_Rod_Holder_wEndSwitch.step, Mini12864_Mount.step, xy_endstop_bumper.step]
2025-11-04 Renamed printed_parts to printed parts_old
    Just doing this for safety in case it's a whoopsie.
    [Bottom_frame_side_connector.step, Bottom_front_connector.step, Bottom_front_left.step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]
2025-11-04 Added plated versions of the parts to the github.
    These are plated versions of the parts for version 1 of the Magpie.
    [Bottom_frame_connecting_pieces.stl, Bottom_frame_corner_pieces.stl, Door_parts.stl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]
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2025-11-05 Added plated version of sherpa mini toolhead to folder
    Plated parts for sherpa mini moved from mod to legitimate option with Orbiter 2
    [toolhead_pieces_Orbiter2.stl, toolhead_pieces_Sherpa_mini.stl]
2025-11-10 Added belts to the CAD
    Added belts to the Freecad and step file for the Magpie.
    [Magpie_Rev_1.step]
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2025-11-24 BL Touch Mod and LED Light Bar Mod Added
    [BLTouch_Mount.step, Cam_Mount.step, led_bracket_bar.step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]
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2026-01-02 Added Printable Precision shim
    Added the printable precision shim to the plated parts section. yes, it's printable. No, it's not technically plated.
    Yes, it works to use a printed shim. You may eventually have to replace the shim after its worn down a bunch, but it works very well.
    [printable_precision_shim.step]
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2026-01-11 Fixed Error on page 30, thanks Murphy's Law
    Added markings to denote that TWO stepper motors are used in the X and Y motion on page 30 of the in progress build guide.
2026-01-11 Update X&Y_Motion_Parts.stl
    Flipped the Y-carriages so they don't require support. I had mistakenly oriented them incorrectly on the build plate on first publishing.
    [X&Y_Motion_Parts.stl]
2026-01-13 Increased hole size for screws
    Increased hole size for screws on the front rod holder, rear rod holder, and y clamps.
    Also updated the plated parts to reflect the change.
    [Magpie_Rev_1.step, X&Y_Motion_Parts.stl]
2026-01-15 Added a rear beefy coupler since there wasn't one.
    [beefy_rear_coupler.step]
2026-01-15 Added pages to build guide, adjusted holes in CAD, added screws.
    Thanks, Murphy's law
    [Magpie_Rev_1.step]
2026-01-16 Renamed lengths of extrusion, as they were mislabeled.
    [Magpie_Rev_1.step]
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2026-01-18 Strengthened Left Y carriage.
    The left Y carriage was weak because it was too thin at the top. For fear of belt tension snapping it, I thickened it.
    [Magpie_Rev_1.step, X&Y_Motion_Parts.stl]
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2026-02-02 Add mod: Test Calibration Cube (issue #1)
    [cube.stl]
2026-02-03 Add mod from issue #4
    [cube.stl]
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2026-02-03 Add mod from issue #17
    [spool_holder-Spool_holder.step]
2026-02-04 Add mod from issue #21
    [BTT e3 SKR mini_mount.step, raspberry_pi_5_mount.step, u2c mount.step]
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2026-02-24 Fixed major issues with build guide pages being mislabeled in the z-axis section.
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2026-05-11 Fix image link in Bowden Tube Holder readme
    Updated image URL for the Bowden Tube Holder readme.
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2026-05-11 Fix image links in README.md of mini 12864 mounting bracket
    Updated image links to use direct URLs instead of relative paths.
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2026-05-11 Fix image links in Z-Axis Lead Screw Mod README
    Updated image links in README to use direct URLs instead of relative paths.
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
